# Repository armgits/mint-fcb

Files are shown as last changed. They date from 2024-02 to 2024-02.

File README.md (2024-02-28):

# Mint

Mint Flight Controller Board is compact under a 27 mm square to fit on Micro/Nano class drones using a standard 20 x 20 mm mount. Despite the small form factor, it features a comprehensive set of IO interfaces for a wide range of peripherals.

This repository hosts the KiCAD project of the flight controller board.

> - The PCB design is still under completion. This board has never been built and tested.
> - Firmware for this target does not exist yet.

## Specifications

- **Processor and Sensors**
  - STM32H723VIH6 MCU
  - ICM20602 and BMI088 IMUs
  - DPS310 Barometer

- **Interfaces**
  - 10x PWM outputs (8 for motors and 2 for peripherals)
  - 1x RC input (UART 1)
  - 1x I2C bus for external sensors
  - 1x CAN bus for external sensors
  - 5x UARTs
  - 4-in-1 ESC interface for Motor outputs 1-4
  - DJI Air Unit interface (UART 8)
  - 3x GPIO pins
  - 1x microSD card slot for logging

- **Power**
  - 4V - 32V voltage input (2S-7S)
  - Onboard 5V, 2A BEC for low-power peripherals

- **Physical Dimensions**
  - 26.5 x 26.25 mm
  - 20 x 20 mm, M2 mount pattern

## Images

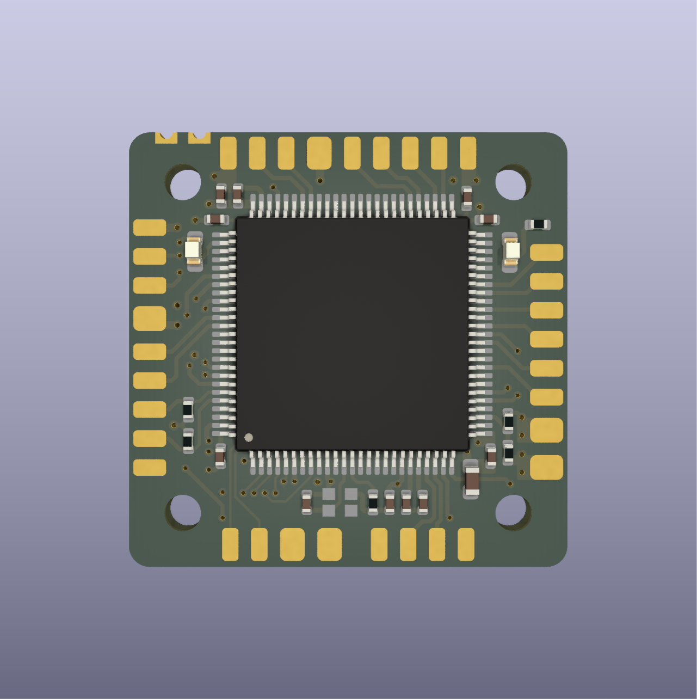
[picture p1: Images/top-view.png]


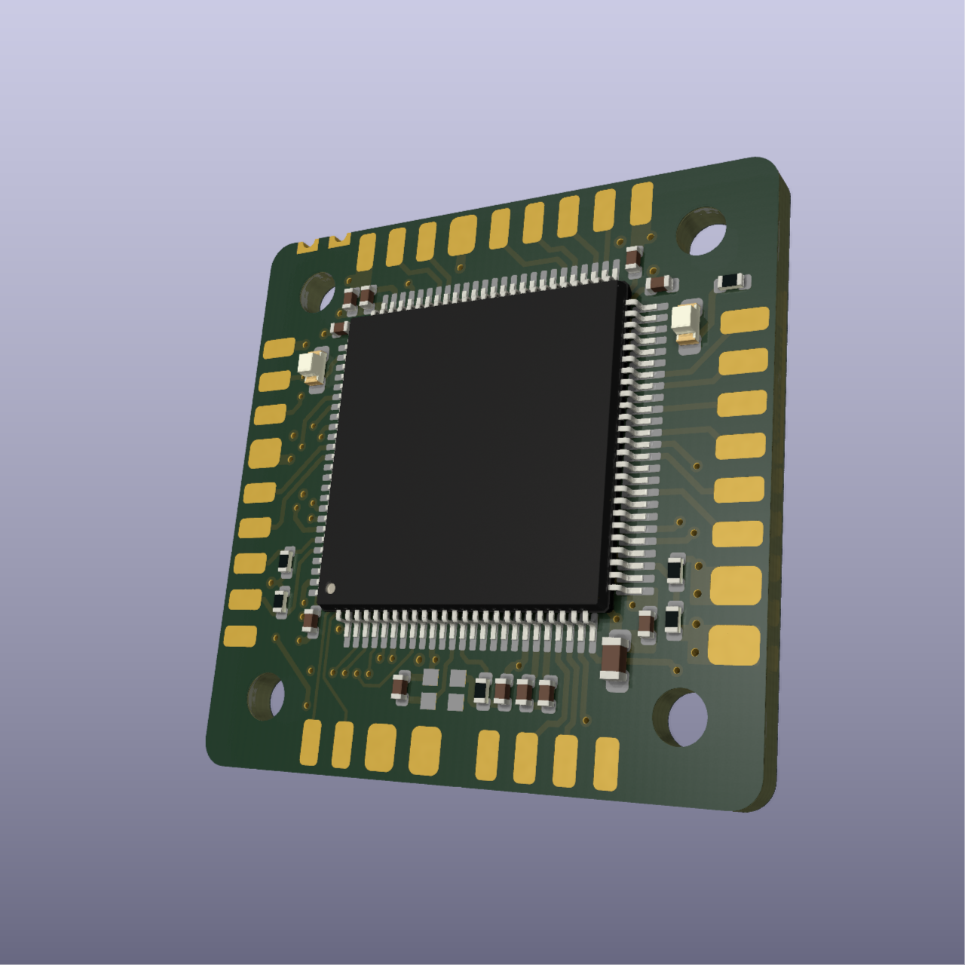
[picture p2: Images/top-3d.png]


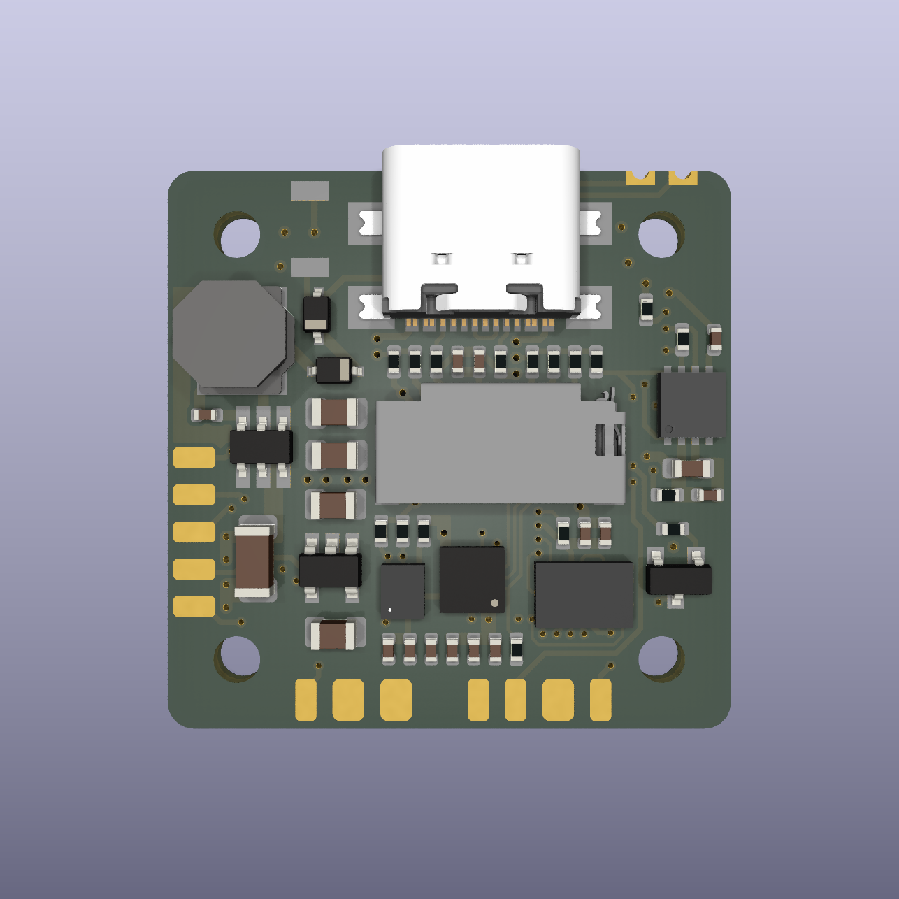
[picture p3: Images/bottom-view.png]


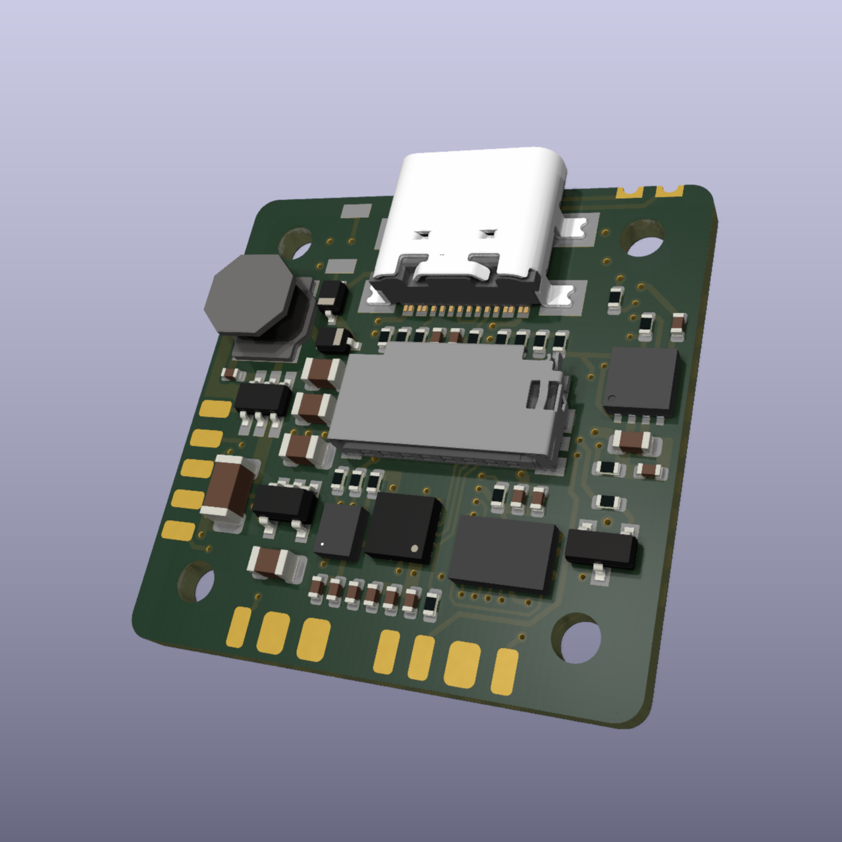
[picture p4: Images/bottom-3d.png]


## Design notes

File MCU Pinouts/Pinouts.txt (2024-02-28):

ADCs: 3
ADC1_INP18 - Voltage
ADC1_INP9 - Current
ADC1_INP16 - General Purpose

SPIs: 3
SPI1 - ICM20602
SPI4 - BMI088

UARTs: 7
PA11 & PA12 - USB
UART1 - Radio RX
UART2 - GPS
UART3 - Spare (With flow control)
UART7 - ESC
UART8 - VTX

I2Cs: 2
I2C1 - External sensors
I2C2 - On board sensors

CANs: 1
CAN1 - External sensors
CAN1 Silent Mode - PD3

SD Card Slots:
SDMMC1

Timers: 6
TIM1 - CH1, CH2, CH3, CH4 (Primary, Motors)
TIM3 - CH2, CH1 (Secondary, Motors)
TIM2 - CH1, CH4 (Secondary, Motors)

TIM4 - CH2 (LED Strip)
TIM16 - CH1N (Buzzer [Just GPIO for Betaflight/INAV])

CS Pins:
ICM20602 - PC1
BMI088-GY - PC13
BMI088-AC - PC14

DRDY(INT) Pins:
ICM20602 - PC2
BMI088-GY1 - PE3
BMI088-GY2 - PE4
BMI088-ACC1 - PC15
BMI088-ACC2 - PC0

GPIO Pins:
LED0 - PA15
PINIO1 - PA1
PINIO2 - PA2

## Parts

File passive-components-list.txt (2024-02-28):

Parts:

----CAPACITORS
0402 8pF 50V Capacitor - GJM1555C1H8R0CB01D
0402 10pF 50V Capacitor - GJM1555C1H100JB01D
0402 47pF 50V Capacitor - C0402C470K5GACTU
0402 2.2nF 50V Capacitor - C0402C222K5RACTU
0402 10nF 50V Capacitor - UMF105B7103MVHF
0402 100nF 16V Capacitor - C0402C104K4RAC7411
0402 1uF 10V Capacitor - LMK105BJ105MVHF
0402 2.2uF 10V Capacitor - LMK105BJ225KV-F

0603 4.7uF 10V Capacitor - LMK107BJ475MAHT
0603 22uF 10V Capacitor - CL10A226MPCNUBE

0805 100nF 50V Capacitor - C0805C104M5RACTU
0805 10uF 35V Capacitor - GRM21BR6YA106ME43L
0805 22uF 10V Capacitor - GRM21BR61A226ME51L

1206 10uF 50V Capacitor - UMK316BBJ106KL-T
1206 22uF 25V Capacitor - CL31A226KAHNNNE

----RESISTORS
0402 120ohm 75V Resistor - CRCW0603120RFKEAC
0402 1Kohm 50V Resistor - RC0402FR-071KL
0402 47ohm 50V Resistor - RC0402FR-0747RL
0402 10Kohm 50V Resistor - RC0402FR-0710KL
0402 100Kohm 50V Resistor - RC0402FR-07100KL
0402 220ohm 50V Resistor - RC0402FR-07220RL
0402 1.5Kohm 50V Resistor - RC0402FR-071K5L
0402 2Kohm 50V Resistor - RC0402FR-072KL
0402 5.1KOhm 50V Resistor - RC0402FR-075K1L
0402 75ohm 50V Resistor - RC0402FR-0775RL

0603 30ohm 75V Resistor - RC0603FR-0730RL
0603 52.3Kohm 75V Resistor - RC0603FR-1052K3L
0603 10Kohm 75V Resistor - RC0603FR-0710KL
0603 30.1Kohm 75V Resistor - RC0603FR-0730K1L
0603 100Kohm 75V Resistor - RC0603FR-07100KL
0603 158Kohm 75V Resistor - RC0603FR-07158KL
0603 7.15Kohm 75V Resistor - ERJ-3EKF7151V

----DIODES
SMC(DO-214AB) 40V 3A Schottky Diode - B340-13-F
SOD-323-2 10V 3A Schottky Diode - BAT 60A E6327

0603 Green LED - KP DELMS1.22-MGNH-25-E6L6
0603 Orange LED - KO DELLS1.22-KHLI-24

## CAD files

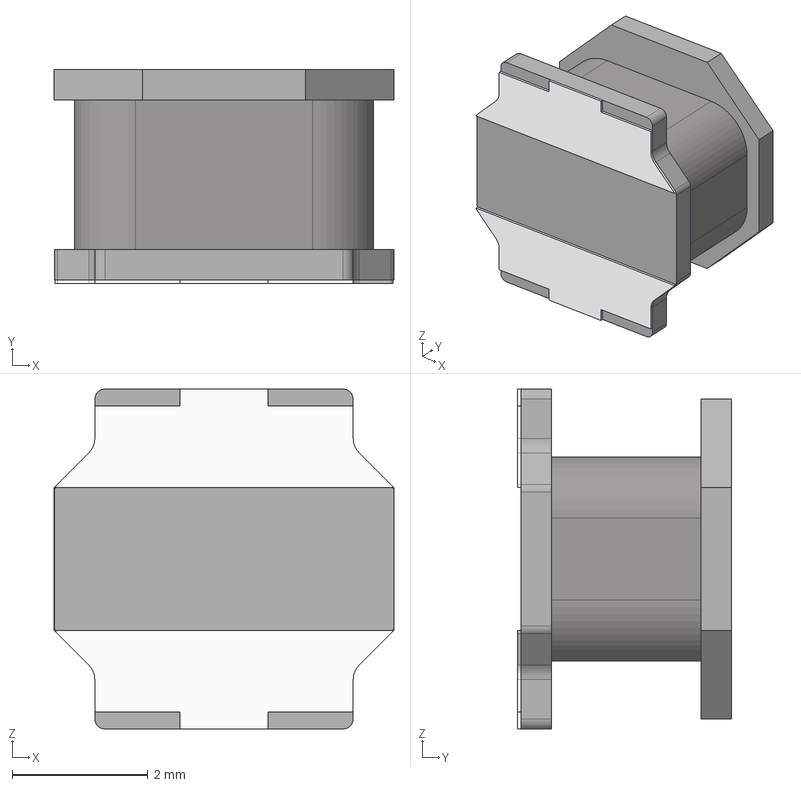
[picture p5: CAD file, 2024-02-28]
Imported 3D Models/NRS5030T4R7MMGJ.step
5.00 x 3.15 x 5.00 mm

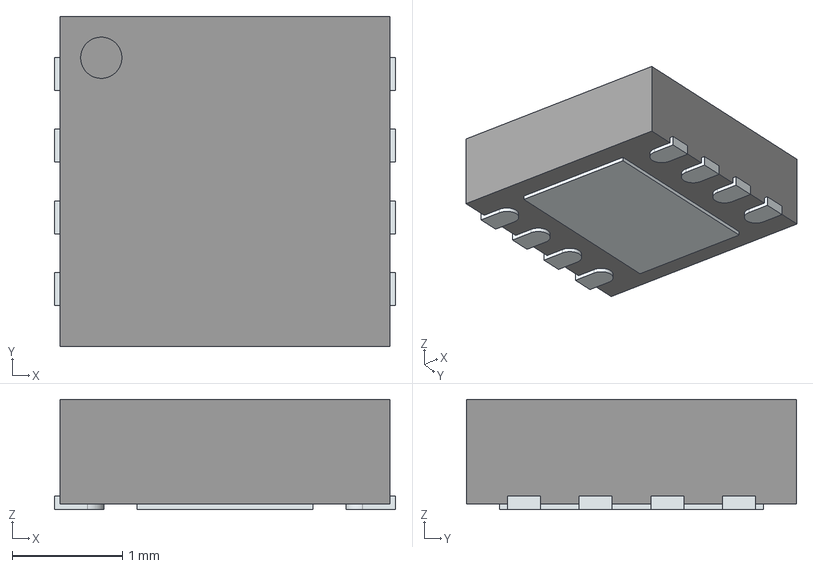
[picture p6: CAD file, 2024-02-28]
Imported 3D Models/TCAN1051GVDRBRQ1.stp
3.10 x 3.00 x 1.00 mm
ThermalPin
PinsArrayLR

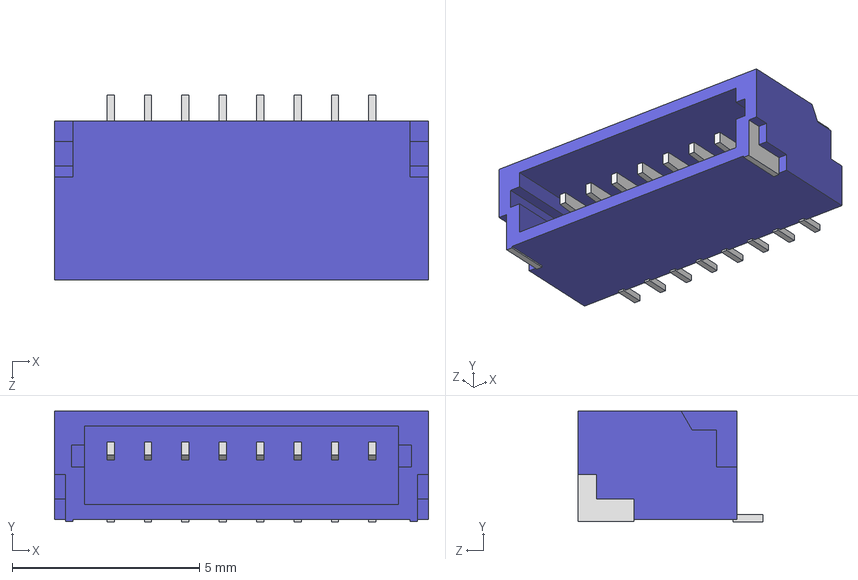
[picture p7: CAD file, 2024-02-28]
Imported 3D Models/SM08B-SRSS-TB.STEP
10.0 x 2.96 x 4.95 mm

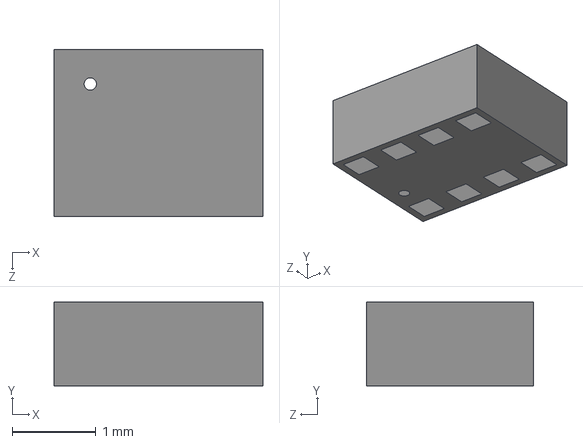
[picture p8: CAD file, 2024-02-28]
Imported 3D Models/DPS310XTSA1.STEP
2.50 x 1.00 x 2.00 mm

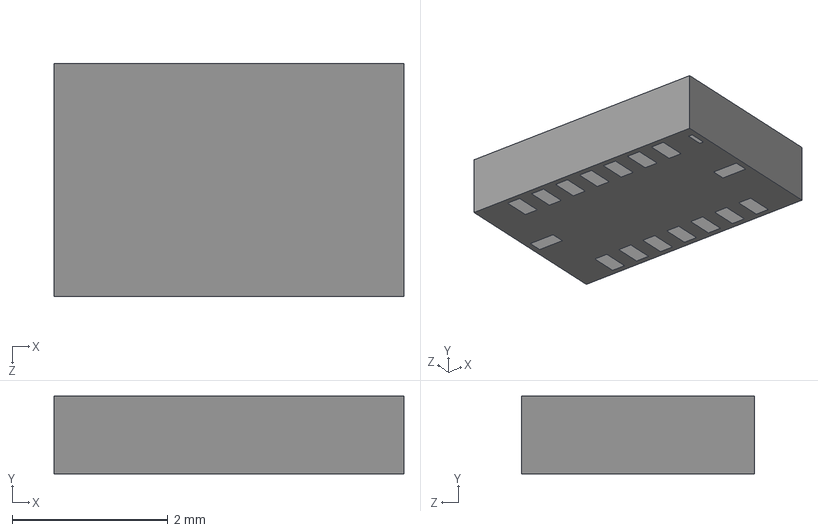
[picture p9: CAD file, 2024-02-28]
Imported 3D Models/BMI088.STEP
4.50 x 1.00 x 3.00 mm

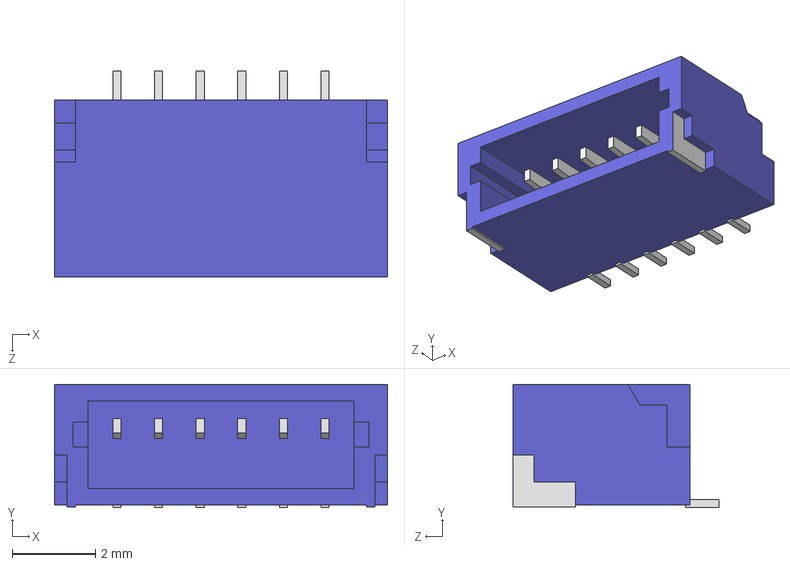
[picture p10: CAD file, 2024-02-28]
Imported 3D Models/SM06B-SRSS-TB.STEP
8.00 x 2.96 x 4.95 mm

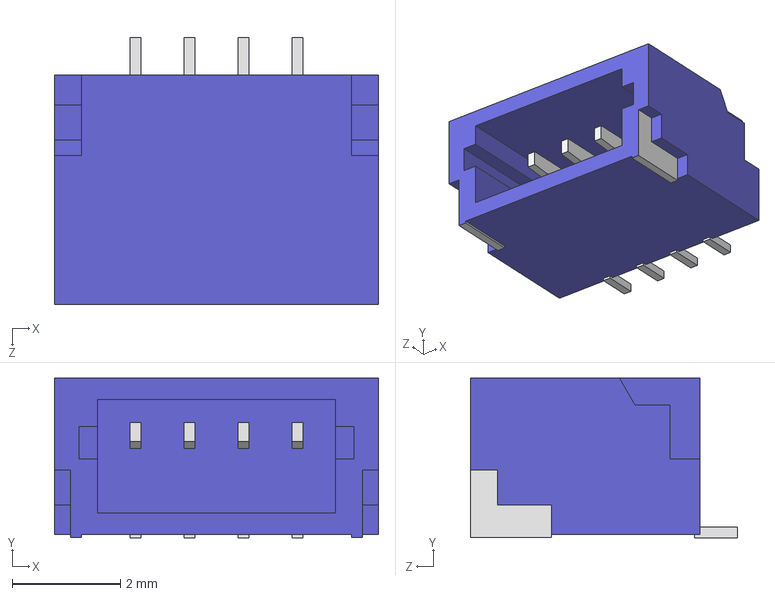
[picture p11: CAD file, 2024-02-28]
Imported 3D Models/SM04B-SRSS-TB.STEP
6.00 x 2.96 x 4.95 mm

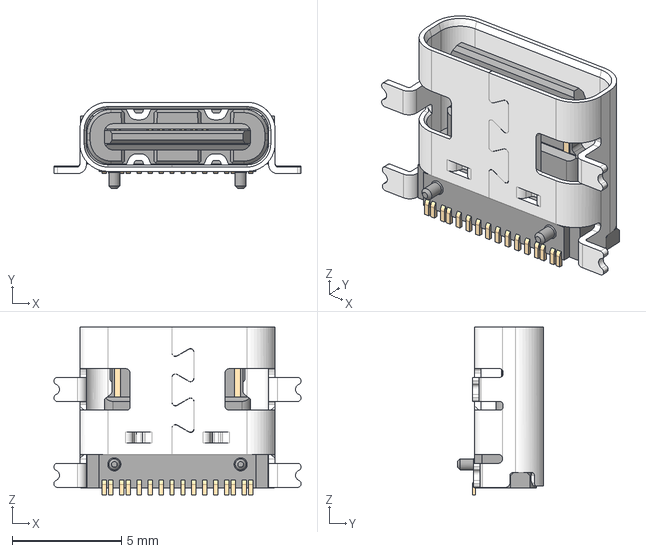
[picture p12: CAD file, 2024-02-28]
Imported 3D Models/USB4110-GF-A.stp
11.3 x 3.96 x 7.68 mm

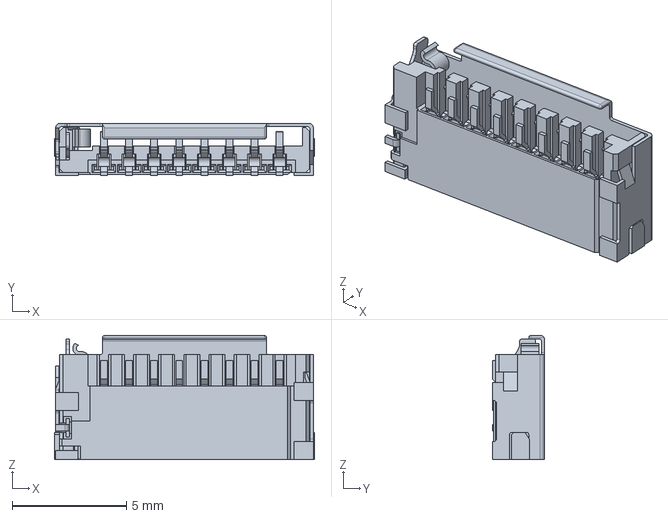
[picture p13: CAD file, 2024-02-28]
Imported 3D Models/475710001.stp
11.4 x 2.30 x 5.45 mm

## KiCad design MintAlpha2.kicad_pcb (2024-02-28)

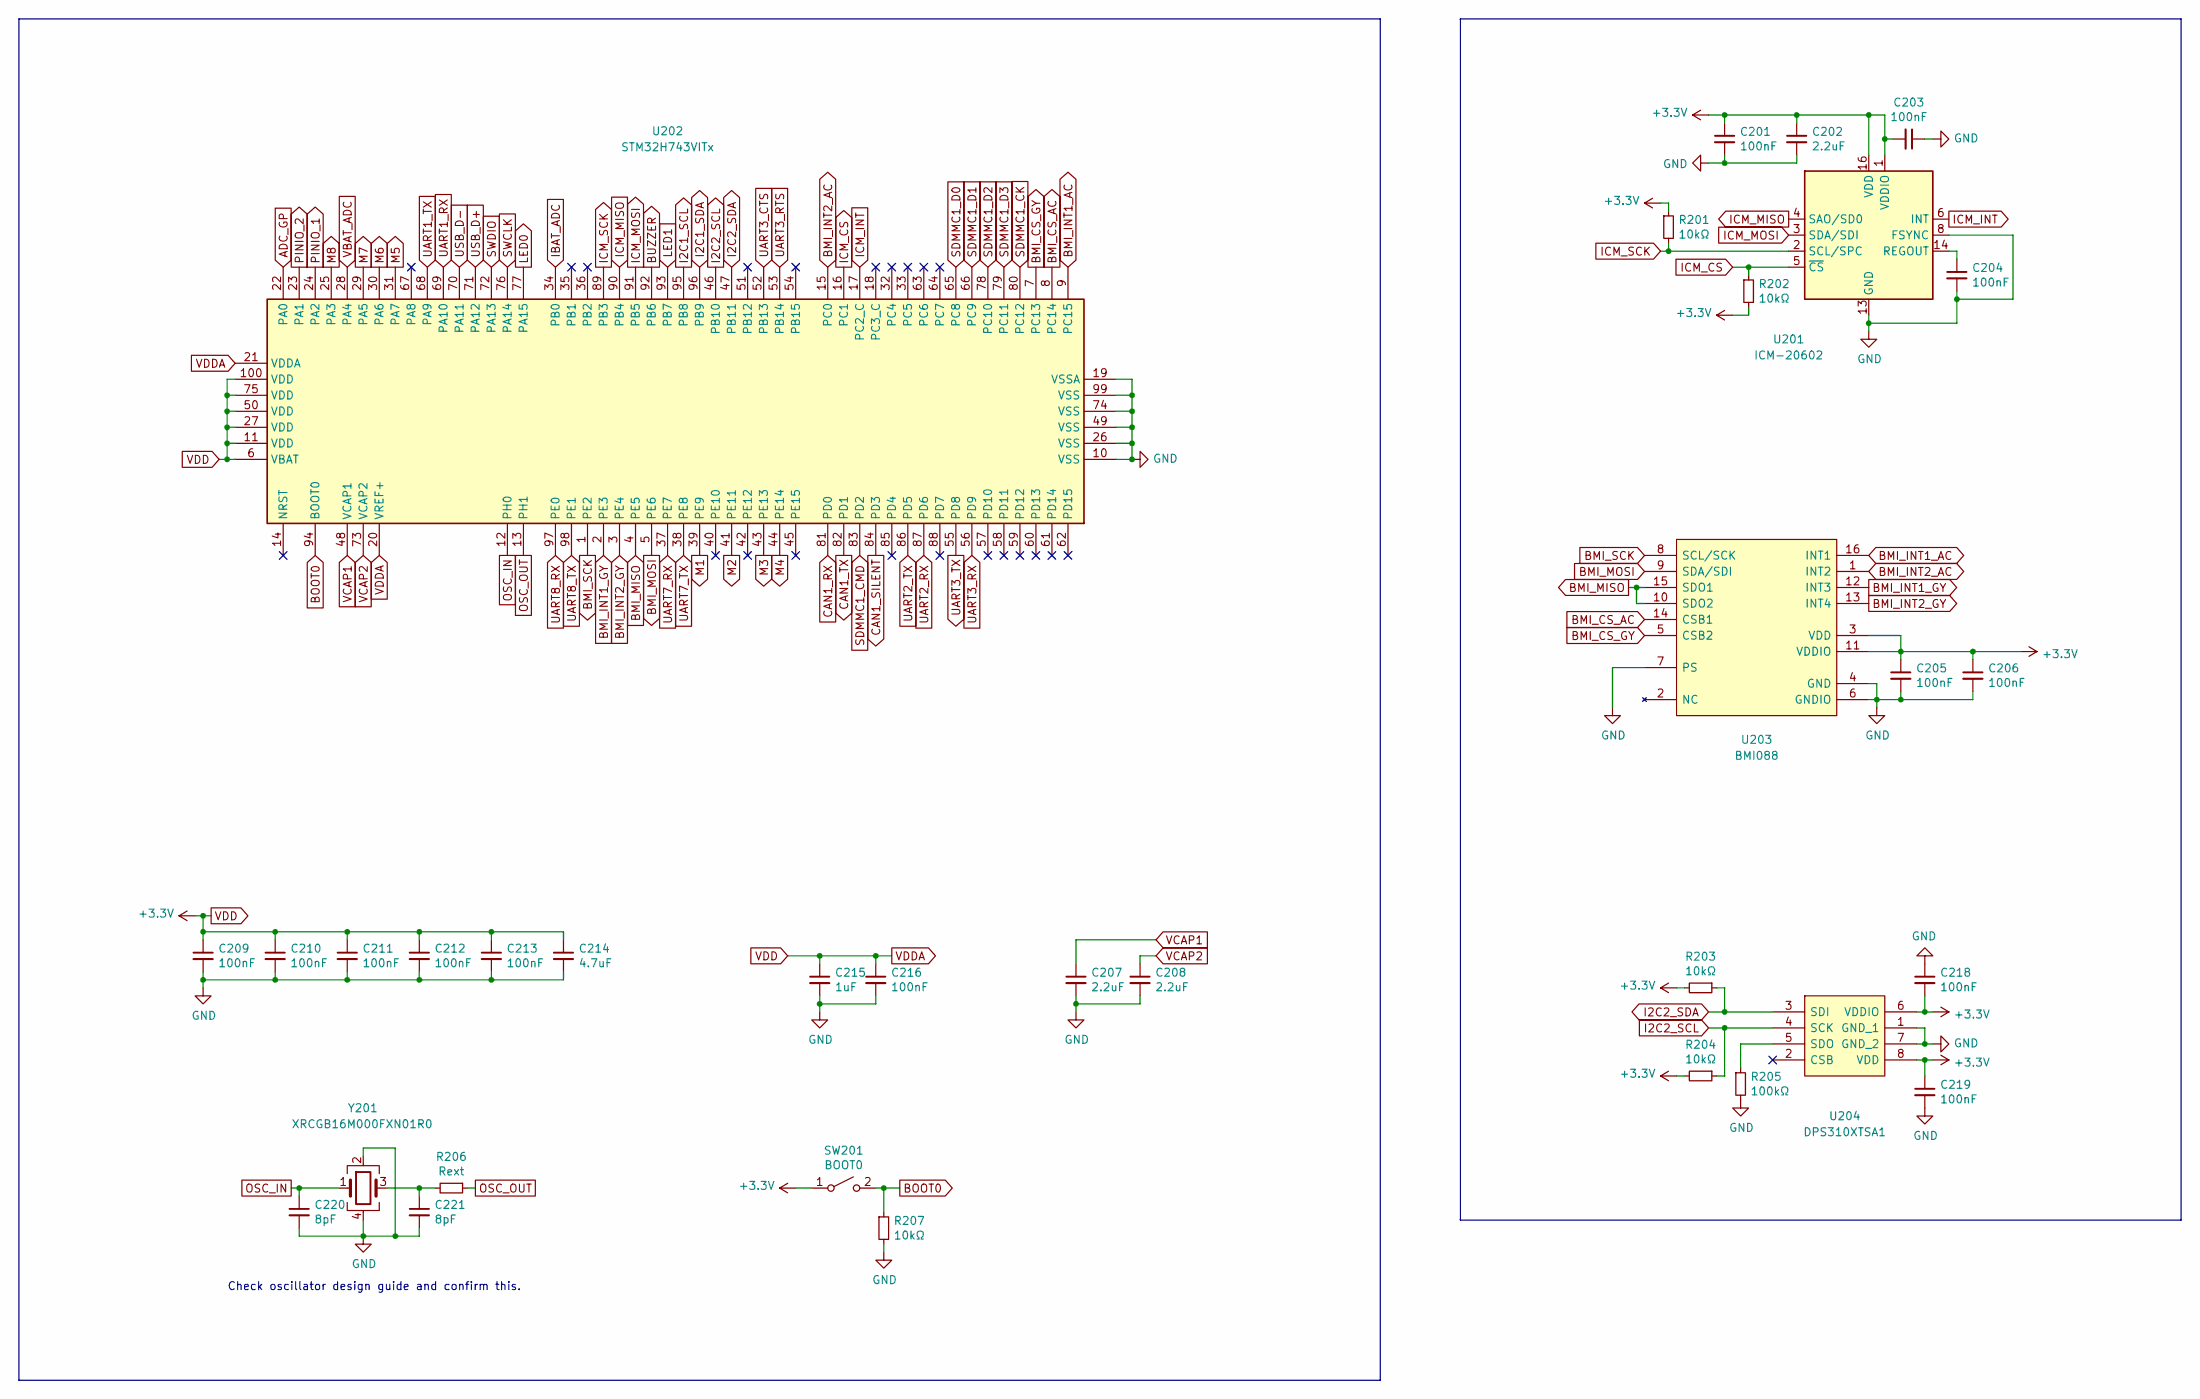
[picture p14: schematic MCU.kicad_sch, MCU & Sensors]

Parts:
C201, C203, C204, C205, C206, C209, C210, C211, C212, C213, C216, C218, C219: 100nF; C_0402_1005Metric; Part No. C0402C104K4RAC7411
C202, C207, C208: 2.2uF; C_0402_1005Metric; Part No. LMK105BJ225KV-F
C214: 4.7uF; C_0603_1608Metric; Part No. LMK107BJ475MAHT
C215: 1uF; C_0402_1005Metric; Part No. LMK105BJ105MVHF
C220, C221: 8pF; C_0402_1005Metric; Part No. GJM1555C1H8R0CB01D
R201, R202, R203, R204, R207: 10kΩ; R_0402_1005Metric; Part No. RC0402FR-0710KL
R205: 100kΩ; R_0402_1005Metric; Part No. RC0402FR-07100KL
R206: Rext; R_0402_1005Metric
SW201: BOOT0; TactileSwitch_B3U-1000P_SPST_NO; Part No. KMS233GLFG
U201: ICM-20602; LGA-16_3x3mm_P0.5mm_LayoutBorder3x5y; Part No. ICM-20602
U202: STM32H743VITx; LQFP-100_14x14mm_P0.5mm
U203: BMI088; BMI088_LGA16_4.5x3mm_P0.5mm; Part No. BMI088
U204: DPS310XTSA1; DPS310_PG-VLGA-8-1; Part No. DPS310XTSA1
Y201: XRCGB16M000FXN01R0; Crystal_Murata_XRCGB_F_P_HCR2016; Part No. XRCGB16M000FXN01R0

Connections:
ADC_GP: U202.22 (PA0); also elsewhere on the board
BMI_CS_AC: U202.8 (PC14), U203.14 (CSB1)
BMI_CS_GY: U202.7 (PC13), U203.5 (CSB2)
BMI_INT1_AC: U202.9 (PC15), U203.16 (INT1)
BMI_INT1_GY: U202.2 (PE3), U203.12 (INT3)
BMI_INT2_AC: U202.15 (PC0), U203.1 (INT2)
BMI_INT2_GY: U202.3 (PE4), U203.13 (INT4)
BMI_MISO: U202.4 (PE5), U203.10 (SDO2), U203.15 (SDO1)
BMI_MOSI: U202.5 (PE6), U203.9 (SDA/SDI)
BMI_SCK: U202.1 (PE2), U203.8 (SCL/SCK)
BOOT0: R207.1, SW201.2 (B), U202.94 (BOOT0)
BUZZER: U202.92 (PB6); also elsewhere on the board
CAN1_RX: U202.81 (PD0); also elsewhere on the board
CAN1_SILENT: U202.84 (PD3); also elsewhere on the board
CAN1_TX: U202.82 (PD1); also elsewhere on the board
GND: C201.2, C202.2, C203.1, C204.2, C205.2, C206.2, C207.2, C208.2, C209.2, C210.2, C211.2, C212.2, C213.2, C214.2, C215.2, C216.2, C218.1, C219.2, C220.2, C221.2, R205.2, R207.2, U201.8 (FSYNC), U201.9 (GND), U201.10 (GND), U201.11 (GND), U201.12 (GND), U201.13 (GND), U201.15 (GND), U202.10 (VSS), U202.19 (VSSA), U202.26 (VSS), U202.49 (VSS), U202.74 (VSS), U202.99 (VSS), U203.4 (GND), U203.6 (GNDIO), U203.7 (PS), U204.1 (GND_1), U204.7 (GND_2), Y201.2, Y201.4; also elsewhere on the board
I2C1_SCL: U202.95 (PB8); also elsewhere on the board
I2C1_SDA: U202.96 (PB9); also elsewhere on the board
I2C2_SCL: R204.1, U202.46 (PB10), U204.4 (SCK)
I2C2_SDA: R203.1, U202.47 (PB11), U204.3 (SDI)
IBAT_ADC: U202.34 (PB0); also elsewhere on the board
ICM_CS: R202.1, U201.5 (~CS), U202.16 (PC1)
ICM_INT: U201.6 (INT), U202.17 (PC2_C)
ICM_MISO: U201.4 (SAO/SD0), U202.90 (PB4)
ICM_MOSI: U201.3 (SDA/SDI), U202.91 (PB5)
ICM_SCK: R201.2, U201.2 (SCL/SPC), U202.89 (PB3)
LED0: U202.77 (PA15); also elsewhere on the board
LED1: U202.93 (PB7); also elsewhere on the board
M1: U202.39 (PE9); also elsewhere on the board
M2: U202.41 (PE11); also elsewhere on the board
M3: U202.43 (PE13); also elsewhere on the board
M4: U202.44 (PE14); also elsewhere on the board
M5: U202.31 (PA7); also elsewhere on the board
M6: U202.30 (PA6); also elsewhere on the board
M7: U202.29 (PA5); also elsewhere on the board
M8: U202.25 (PA3); also elsewhere on the board
unnamed: C204.1, U201.14 (REGOUT)
unnamed: C221.1, R206.2, Y201.3
unnamed: R205.1, U204.5 (SDO)
OSC_IN: C220.1, U202.12 (PH0), Y201.1
OSC_OUT: R206.1, U202.13 (PH1)
PINIO_1: U202.24 (PA2); also elsewhere on the board
PINIO_2: U202.23 (PA1); also elsewhere on the board
SDMMC1_CK: U202.80 (PC12); also elsewhere on the board
SDMMC1_CMD: U202.83 (PD2); also elsewhere on the board
SDMMC1_D0: U202.65 (PC8); also elsewhere on the board
SDMMC1_D1: U202.66 (PC9); also elsewhere on the board
SDMMC1_D2: U202.78 (PC10); also elsewhere on the board
SDMMC1_D3: U202.79 (PC11); also elsewhere on the board
SWCLK: U202.76 (PA14); also elsewhere on the board
SWDIO: U202.72 (PA13); also elsewhere on the board
UART1_RX: U202.69 (PA10); also elsewhere on the board
UART1_TX: U202.68 (PA9); also elsewhere on the board
UART2_RX: U202.87 (PD6); also elsewhere on the board
UART2_TX: U202.86 (PD5); also elsewhere on the board
UART3_CTS: U202.52 (PB13); also elsewhere on the board
UART3_RTS: U202.53 (PB14); also elsewhere on the board
UART3_RX: U202.56 (PD9); also elsewhere on the board
UART3_TX: U202.55 (PD8); also elsewhere on the board
UART7_RX: U202.37 (PE7); also elsewhere on the board
UART7_TX: U202.38 (PE8); also elsewhere on the board
UART8_RX: U202.97 (PE0); also elsewhere on the board
UART8_TX: U202.98 (PE1); also elsewhere on the board
USB_D+: U202.71 (PA12); also elsewhere on the board
USB_D-: U202.70 (PA11); also elsewhere on the board
VBAT_ADC: U202.28 (PA4); also elsewhere on the board
VCAP1: C207.1, U202.48 (VCAP1)
VCAP2: C208.1, U202.73 (VCAP2)
VDD: C201.1, C202.1, C203.2, C205.1, C206.1, C209.1, C210.1, C211.1, C212.1, C213.1, C214.1, C215.1, C216.1, C218.2, C219.1, R201.1, R202.2, R203.2, R204.2, SW201.1 (A), U201.1 (VDDIO), U201.16 (VDD), U202.6 (VBAT), U202.11 (VDD), U202.20 (VREF+), U202.21 (VDDA), U202.27 (VDD), U202.50 (VDD), U202.75 (VDD), U202.100 (VDD), U203.3 (VDD), U203.11 (VDDIO), U204.6 (VDDIO), U204.8 (VDD); also elsewhere on the board

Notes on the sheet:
Check oscillator design guide and confirm this.

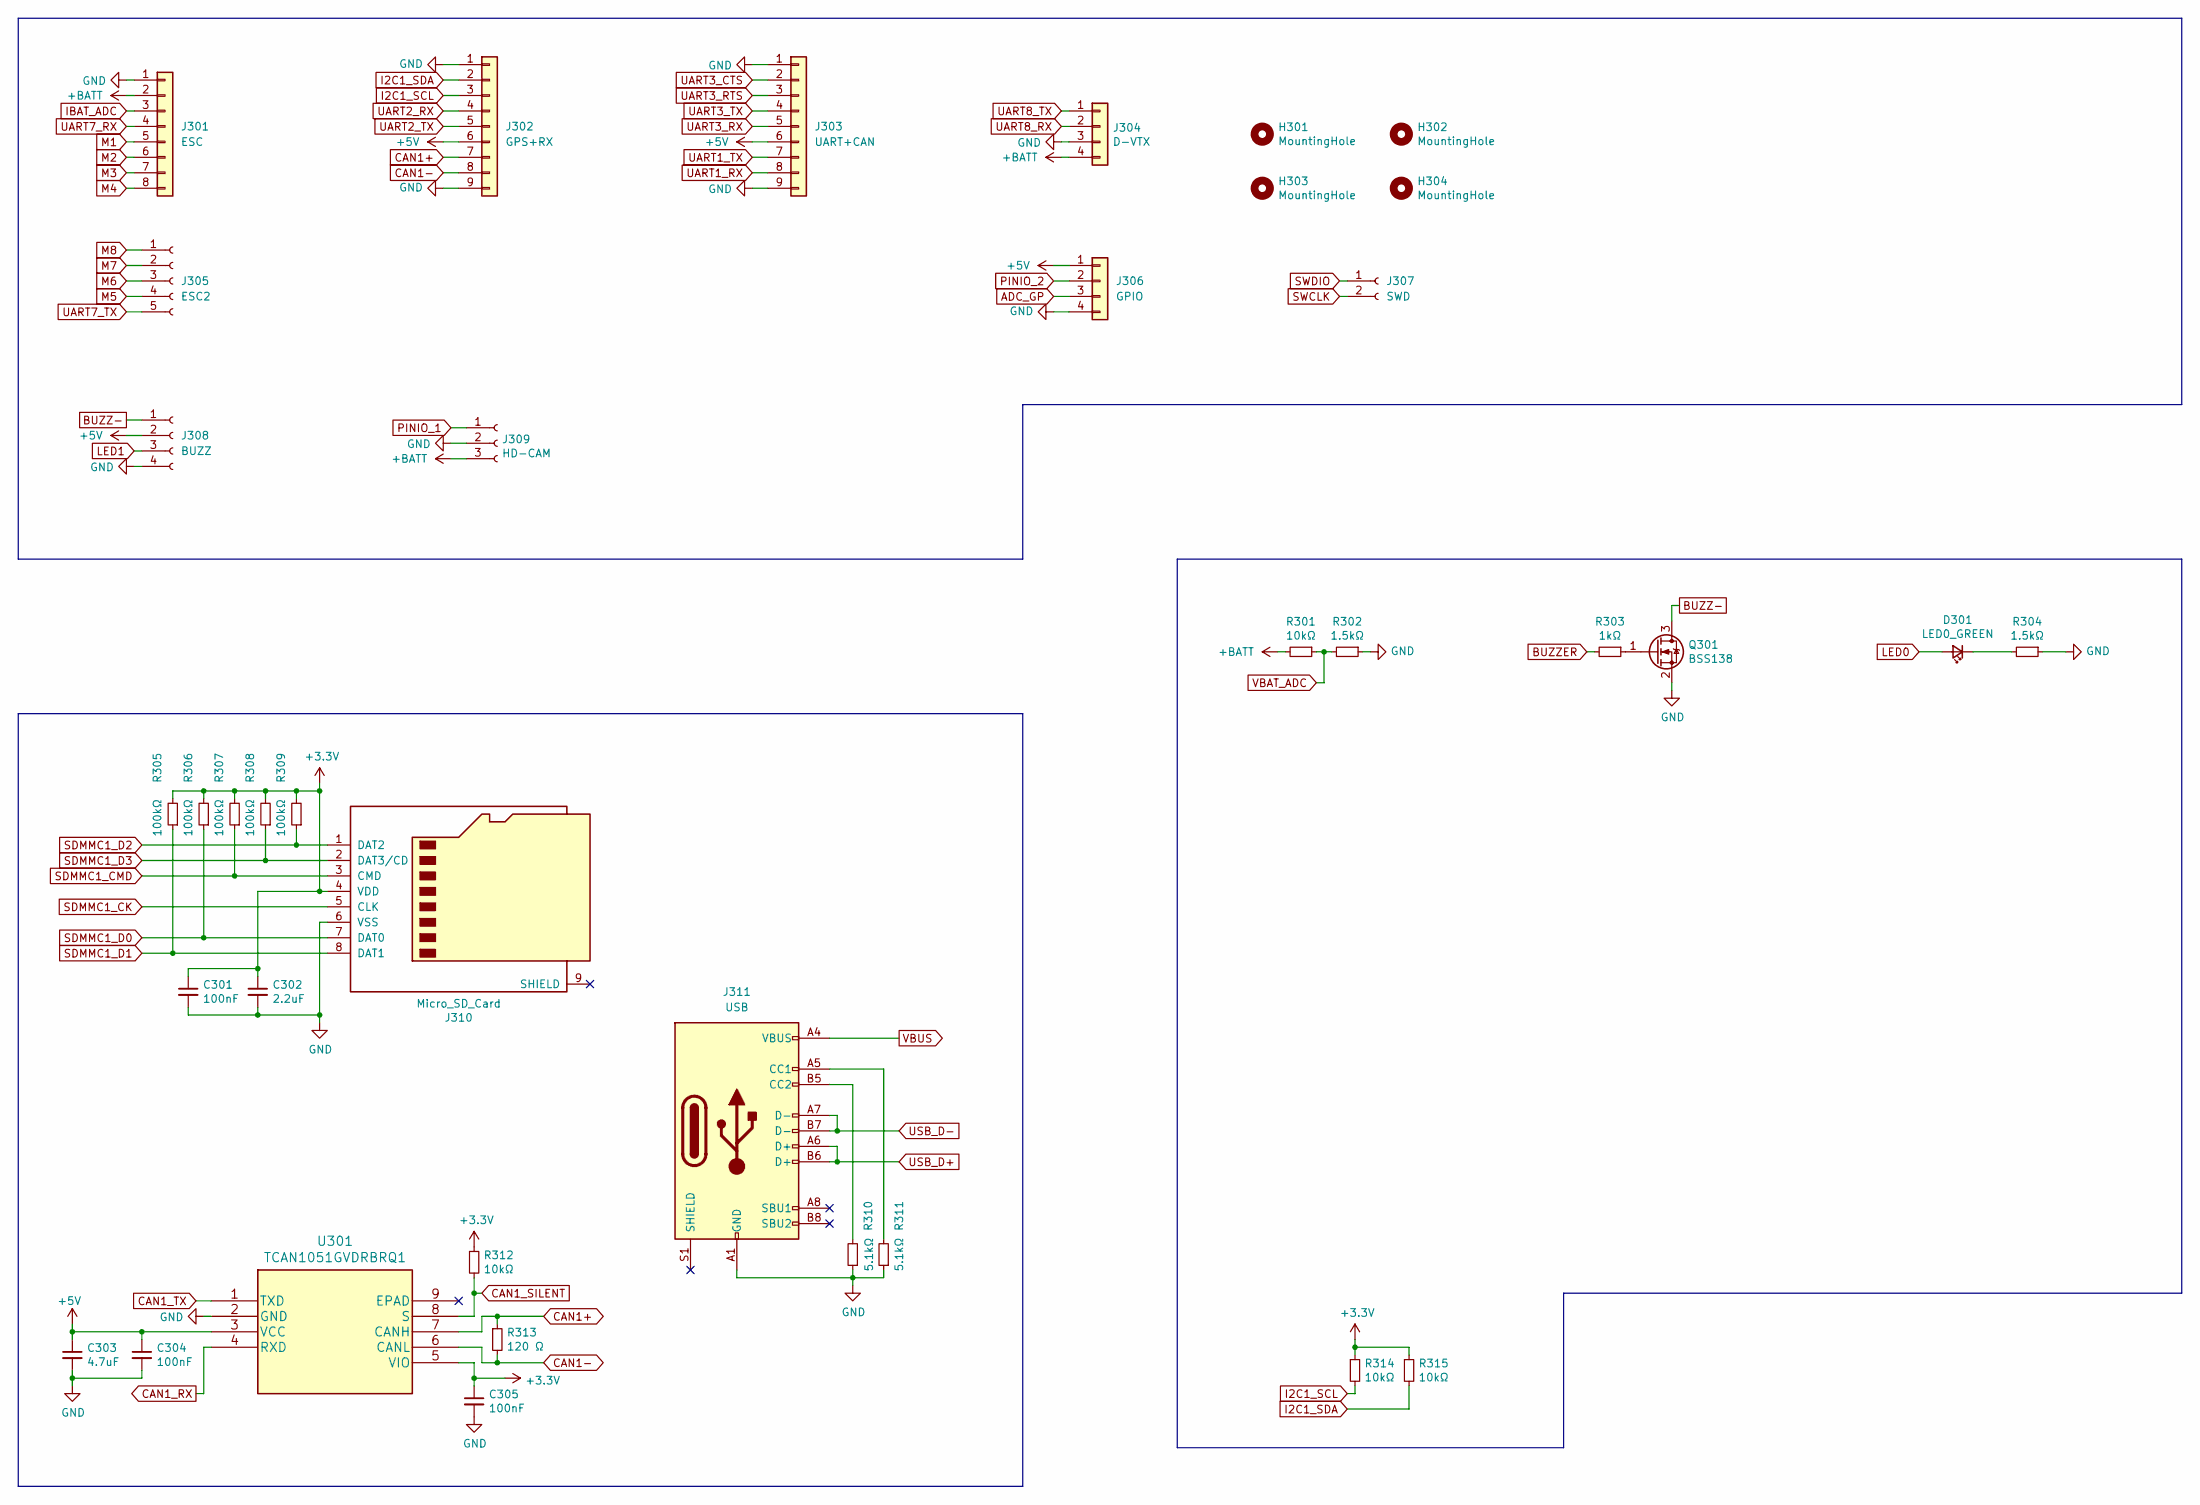
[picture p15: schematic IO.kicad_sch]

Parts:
C301, C304, C305: 100nF; C_0402_1005Metric; Part No. C0402C104K4RAC7411
C302: 2.2uF; C_0402_1005Metric; Part No. LMK105BJ225KV-F
C303: 4.7uF; C_0603_1608Metric; Part No. LMK107BJ475MAHT
D301: LED0_GREEN; LED_0603_1608Metric; Part No. KP DELMS1.22-MGNH-25-E6L6
H301, H302, H303, H304: MountingHole; MountingHole_2.2mm_M2_ISO14580
J301: ESC; CustomSolderpads_8x1_2x1mm_P1.75mm; Part No. SM08B-SRSS-TB(LF)(SN)
J302: GPS+RX; SideSolderpads_9x1_2x1mm_P1.75mm
J303: UART+CAN; SideSolderpads_9x1_2x1mm_P1.75mm
J304: D-VTX; CustomSolderpads_4x1_2x1mm_P1.75mm; Part No. SM06B-SRSS-TB(LF)(SN)
J305: ESC2; Solderpads_5x1_2x1mm_P1.75mm
J306: GPIO; Solderpads_4x1_2x1mm_P1.75mm
J307: SWD; CustomPinHeader_1x02_P2.00mm_Vertical
J308: BUZZ; SideSolderpads_4x1_2x1mm_P1.75mm
J309: HD-CAM; CustomSolderpads_3x1_2x1mm_P1.75mm
J310: Micro_SD_Card; MicroSD_Molex_475710001; Part No. 47571-0001
J311: USB; USB-C_GF-USB4110; Part No. USB4110-GF-A
Q301: BSS138; SOT-23
R301, R312, R314, R315: 10kΩ; R_0402_1005Metric; Part No. RC0402FR-0710KL
R302, R304: 1.5kΩ; R_0402_1005Metric; Part No. RC0402FR-071K5L
R303: 1kΩ; R_0402_1005Metric; Part No. RC0402FR-071KL
R305, R306, R307, R308, R309: 100kΩ; R_0402_1005Metric; Part No. RC0402FR-07100KL
R310, R311: 5.1kΩ; R_0402_1005Metric; Part No. RC0402FR-075K1L
R313: 120 Ω; R_0402_1005Metric; Part No. CRCW0603120RFKEAC
U301: TCAN1051GVDRBRQ1; Part No. TCAN1051GVDRBRQ1

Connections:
+5V: C303.1, C304.1, J302.6, J303.6, J306.1, J308.2, U301.3 (VCC); also elsewhere on the board
+BATT: J301.2, J304.4, J309.3, R301.2; also elsewhere on the board
ADC_GP: J306.3; also elsewhere on the board
BUZZ-: J308.1, Q301.3 (D)
BUZZER: R303.2; also elsewhere on the board
CAN1+: J302.7, R313.1, U301.7 (CANH)
CAN1-: J302.8, R313.2, U301.6 (CANL)
CAN1_RX: U301.4 (RXD); also elsewhere on the board
CAN1_SILENT: R312.2, U301.8 (S); also elsewhere on the board
CAN1_TX: U301.1 (TXD); also elsewhere on the board
GND: C301.2, C302.2, C303.2, C304.2, C305.2, J301.1, J302.1, J302.9, J303.1, J303.9, J304.3, J306.4, J308.4, J309.2, J310.6 (VSS), J311.A1 (GND), J311.A12 (GND), J311.B1 (GND), J311.B12 (GND), Q301.2 (S), R302.1, R304.1, R310.1, R311.1, U301.2 (GND); also elsewhere on the board
I2C1_SCL: J302.3, R314.2; also elsewhere on the board
I2C1_SDA: J302.2, R315.2; also elsewhere on the board
IBAT_ADC: J301.3; also elsewhere on the board
LED0: D301.2 (A); also elsewhere on the board
LED1: J308.3; also elsewhere on the board
M1: J301.5; also elsewhere on the board
M2: J301.6; also elsewhere on the board
M3: J301.7; also elsewhere on the board
M4: J301.8; also elsewhere on the board
M5: J305.4; also elsewhere on the board
M6: J305.3; also elsewhere on the board
M7: J305.2; also elsewhere on the board
M8: J305.1; also elsewhere on the board
unnamed: D301.1 (K), R304.2
unnamed: J311.A5 (CC1), R311.2
unnamed: J311.B5 (CC2), R310.2
unnamed: Q301.1 (G), R303.1
PINIO_1: J309.1; also elsewhere on the board
PINIO_2: J306.2; also elsewhere on the board
SDMMC1_CK: J310.5 (CLK); also elsewhere on the board
SDMMC1_CMD: J310.3 (CMD), R307.1; also elsewhere on the board
SDMMC1_D0: J310.7 (DAT0), R306.1; also elsewhere on the board
SDMMC1_D1: J310.8 (DAT1), R305.1; also elsewhere on the board
SDMMC1_D2: J310.1 (DAT2), R309.1; also elsewhere on the board
SDMMC1_D3: J310.2 (DAT3/CD), R308.1; also elsewhere on the board
SWCLK: J307.2; also elsewhere on the board
SWDIO: J307.1; also elsewhere on the board
UART1_RX: J303.8; also elsewhere on the board
UART1_TX: J303.7; also elsewhere on the board
UART2_RX: J302.4; also elsewhere on the board
UART2_TX: J302.5; also elsewhere on the board
UART3_CTS: J303.2; also elsewhere on the board
UART3_RTS: J303.3; also elsewhere on the board
UART3_RX: J303.5; also elsewhere on the board
UART3_TX: J303.4; also elsewhere on the board
UART7_RX: J301.4; also elsewhere on the board
UART7_TX: J305.5; also elsewhere on the board
UART8_RX: J304.2; also elsewhere on the board
UART8_TX: J304.1; also elsewhere on the board
USB_D+: J311.A6 (D+), J311.B6 (D+); also elsewhere on the board
USB_D-: J311.A7 (D-), J311.B7 (D-); also elsewhere on the board
VBAT_ADC: R301.1, R302.2; also elsewhere on the board
VBUS: J311.A4 (VBUS), J311.A9 (VBUS), J311.B4 (VBUS), J311.B9 (VBUS); also elsewhere on the board
VDD: C301.1, C302.1, C305.1, J310.4 (VDD), R305.2, R306.2, R307.2, R308.2, R309.2, R312.1, R314.1, R315.1, U301.5 (VIO); also elsewhere on the board

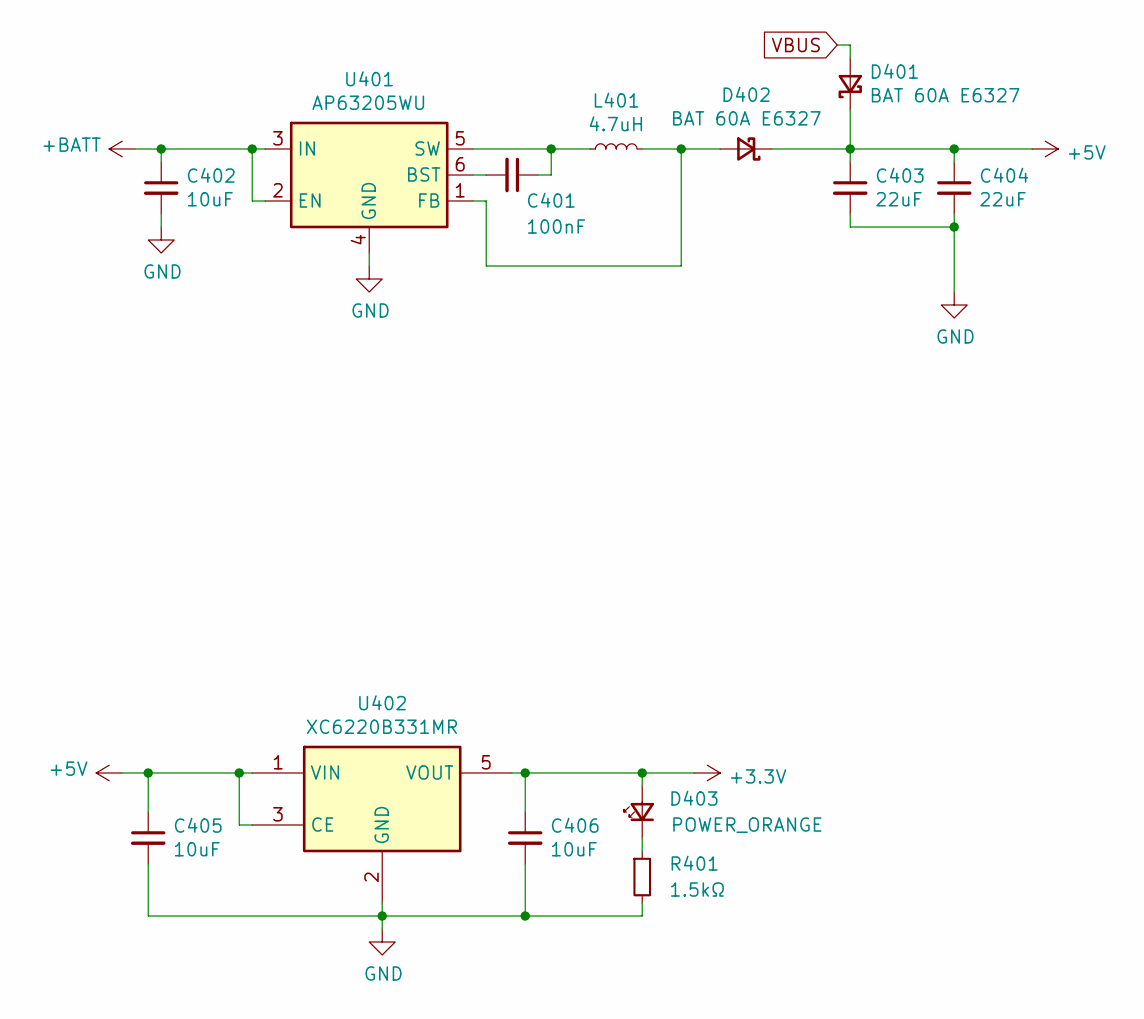
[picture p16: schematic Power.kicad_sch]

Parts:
C401: 100nF; C_0402_1005Metric; Part No. C0402C104K4RAC7411
C402: 10uF; C_1206_3216Metric; Part No. UMK316BBJ106KL-T
C403, C404: 22uF; C_0805_2012Metric; Part No. GRM21BR61A226ME51L
C405, C406: 10uF; C_0805_2012Metric; Part No. GRM21BR61C106KE15K
D401, D402: BAT 60A E6327; D_SOD-323; Part No. BAT 60A E6327
D403: POWER_ORANGE; LED_0603_1608Metric; Part No. KO DELLS1.22-KHLI-24
L401: 4.7uH; L_Taiyo-Yuden_NR-50xx; Part No. NRS5030T4R7MMGJ
R401: 1.5kΩ; R_0402_1005Metric; Part No. RC0402FR-071K5L
U401: AP63205WU; TSOT-23-6
U402: XC6220B331MR; SOT-23-5

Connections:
+5V: C403.1, C404.1, C405.1, D401.1 (K), D402.1 (K), U402.1 (VIN), U402.3 (CE); also elsewhere on the board
+BATT: C402.1, U401.2 (EN), U401.3 (IN); also elsewhere on the board
GND: C402.2, C403.2, C404.2, C405.2, C406.2, R401.2, U401.4 (GND), U402.2 (GND); also elsewhere on the board
unnamed: C401.1, L401.1, U401.5 (SW)
unnamed: C401.2, U401.6 (BST)
unnamed: D402.2 (A), L401.2, U401.1 (FB)
unnamed: D403.1 (K), R401.1
VBUS: D401.2 (A); also elsewhere on the board
VDD: C406.1, D403.2 (A), U402.5 (VOUT); also elsewhere on the board

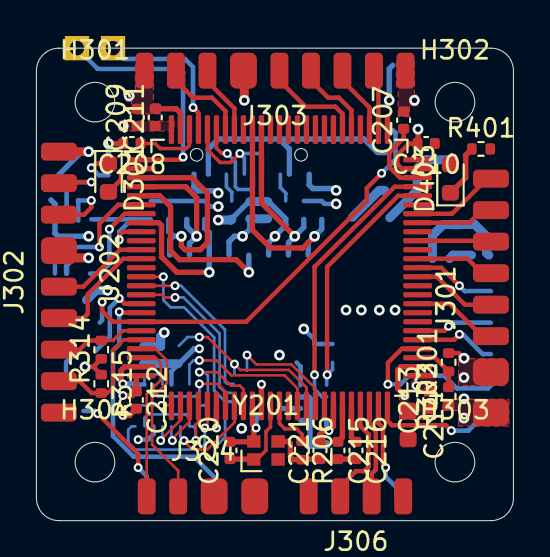
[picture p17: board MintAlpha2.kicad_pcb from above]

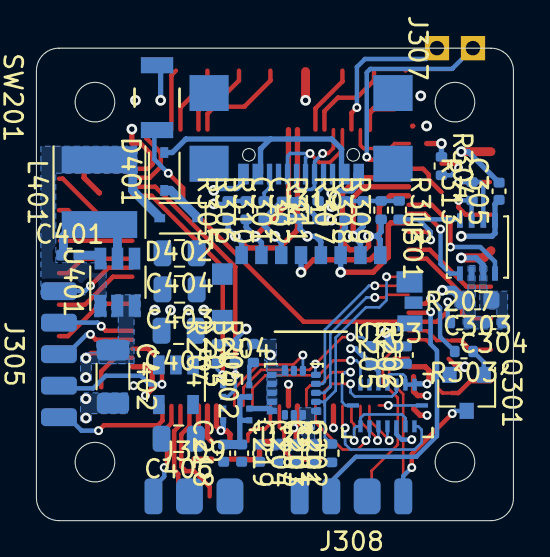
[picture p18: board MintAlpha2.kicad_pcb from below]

Board: 4 copper layers, 26.5 x 26.2 mm, 84 parts (53 on the bottom side), 83 nets.

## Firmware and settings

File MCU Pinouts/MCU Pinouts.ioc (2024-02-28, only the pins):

PC12.Signal=SDMMC1_CK
PB13.Signal=UART5_TX
PD4.Signal=USART2_RTS
PB6.Signal=USART1_TX
PC7.Signal=S_TIM8_CH2
PD0.Signal=FDCAN1_RX
PD8.Signal=USART3_TX
PE5.Signal=SPI4_MISO
PE1.Signal=UART8_TX
PB2.Signal=GPIO_Output
PE9.Signal=S_TIM1_CH1
PE2.Signal=SPI4_SCK
PE10.Signal=GPIO_Output
PA0.Signal=UART4_TX
PB9.Signal=I2C1_SDA
PB1.Signal=GPIO_Output
PD12.Signal=USART3_RTS
PD15.Signal=EVENTOUT
PC13.Signal=EVENTOUT
PD3.Signal=USART2_CTS
PC6.Signal=S_TIM8_CH1
PD1.Signal=FDCAN1_TX
PA9.Signal=GPIO_Input
PB10.Signal=I2C2_SCL
PB14.Signal=S_TIM12_CH1
PA5.Signal=SPI1_SCK
PE14.Signal=S_TIM1_CH4
PE8.Signal=UART7_TX
PA4.Signal=GPIO_Output
PB5.Signal=SPI3_MOSI
PD11.Signal=USART3_CTS
PA11.Signal=USB_OTG_FS_DM
PE3.Signal=EVENTOUT
PD2.Signal=SDMMC1_CMD
PB0.Signal=S_TIM3_CH3
PC1.Signal=ADCx_INP11
Mcu.UserName=STM32H743VIHx
PC10.Signal=SDMMC1_D2
PB11.Signal=I2C2_SDA
PB15.Signal=GPIO_Output
PD13.Signal=S_TIM4_CH2
PA12.Signal=USB_OTG_FS_DP
PC2_C.Signal=GPIO_Output
PE13.Signal=S_TIM1_CH3
PB7.Signal=USART1_RX
PA6.Signal=SPI1_MISO
PC5.Signal=GPIO_Output
PE7.Signal=UART7_RX
PD6.Signal=USART2_RX
PA3.Signal=ADCx_INP15
PC11.Signal=SDMMC1_D3
PC8.Signal=SDMMC1_D0
PC4.Signal=GPIO_Output
PD5.Signal=USART2_TX
PD9.Signal=USART3_RX
PE11.Signal=S_TIM1_CH2
PA1.Signal=UART4_RX
PE6.Signal=SPI4_MOSI
PE0.Signal=UART8_RX
PA2.Signal=ADCx_INP14
PD14.Signal=S_TIM4_CH3
PB8.Signal=I2C1_SCL
PC9.Signal=SDMMC1_D1
PB12.Signal=UART5_RX
PA7.Signal=SPI1_MOSI

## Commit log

2024-02-28 Fixed MCU pinout description
    [Pinouts.csv]
2024-02-28 Removed brackets around voltage range
2024-02-28 Added hole size in mount description
2024-02-28 Fixed a typo in Footprints library name
2024-02-28 Added microSD card slot to interfaces list

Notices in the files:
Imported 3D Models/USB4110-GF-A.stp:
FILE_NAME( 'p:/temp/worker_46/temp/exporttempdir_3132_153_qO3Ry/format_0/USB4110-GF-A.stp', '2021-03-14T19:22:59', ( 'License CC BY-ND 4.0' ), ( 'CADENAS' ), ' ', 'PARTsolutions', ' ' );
